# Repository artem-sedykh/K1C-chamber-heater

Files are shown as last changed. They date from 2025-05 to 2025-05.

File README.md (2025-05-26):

_# K1C-chamber-heater

Постоянно печатаю ABS, так что давно хотел сделать нагреватель камеры, пробовал разные варианты, например [такой](https://www.printables.com/make/2215362) на 24 вольта, выявил несколько проблем  
1. Обдув должен быть от улитки 12030
2. Знать температура нагревателя
3. Горячий воздух должен быть направлен на стекло(стенки плавятся)

Появилось время, наткнулся на видео [NoizieWorks](https://www.youtube.com/watch?v=dcIuKb0kHWA) нагреватель Qidi Plus 4, было принято решение попробовать собрать из него нагреватель для своего K1C  

И так, нам понадобится:

1. [QIDI Plus4 chamber heater](https://aliexpress.ru/item/1005007804483549.html?sku_id=12000042258968076) 4328 ₽.
2. [STM32-Klipper-Expander](https://aliexpress.ru/item/1005002384419036.html?sku_id=12000020472565357) 1359 ₽ плата расширения, доп. выходы, нужна для подключения нагревателя, термистора нагревателя и вентилятора
3. Винты 15x[M3x6 FHCS](https://aliexpress.ru/item/4001072025844.html)
4. Винты 3x[M3x40 FHCS](https://aliexpress.ru/item/4001072025844.html?sku_id=10000014059762471) для крепления вентилятора к корпусу нагревателя
5. Любая термопаста
6. Вплявляемые гайки 18xM3*3*4.5
7. Реле [SSR-40DA](https://aliexpress.ru/item/1005004040211802.html?sku_id=12000031095481981) 349 ₽
8. Провода 14awg протянуть до платы 220в(родных не хватит)
9. Провода для удлинения вентилятора
10. Провода для удлинения термистора
11. Коннектор [jst ph2.0 4pin](https://aliexpress.ru/item/1005008769943807.html) 
12. Обжимка для коннектора jst ph2.0 4pin
13. Кабель micro usb
14. [Набор инструментов для обжима и зачистки наконечников](https://www.ozon.ru/product/nabor-instrumentov-dlya-obzhima-i-zachistki-nakonechnikov-soderzhashchiy-odin-1813569243/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), если хотите обжать провода
15. [Кабельный наконечник НВИ](https://www.ozon.ru/product/kabelnyy-nakonechnik-nvi-dori-nabor-8-160sht-1416852199/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) ну и [пресс клещи ПК-16](https://www.ozon.ru/product/press-kleshchi-pk-16-dlya-mednyh-nakonechnikov-i-gilz-do-16kv-1566599786/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)
16. Катушка [Polymaker Fiberon PA6-GF25](https://fiberon.polymaker.com/product/pa6-gf25/) купить можно на [ozon](https://www.ozon.ru/product/pa6-gf25-fiberon-plastik-polymaker-dlya-3d-printera-1-75-mm-seryy-0-5-kg-1785755210/), у пластика тмпература деформации 190 градусов, кароч крутой материал  ~ 2300₽ за 0.5кг
17. Обычный abs для холодной части я использовал ERYONE ABS Carbon, брал [тут](https://www.ozon.ru/product/plastik-abs-carbon-cf-chernyy-black-dlya-3d-printera-eryone-1kg-1704937868/) ~ 2300₽ за 1кг
18. [Оплетка для проводов](https://www.ozon.ru/product/opletka-kabelnaya-iz-poliestera-zmeinaya-kozha-10-8-20mm-cherno-krasnaya-10m-1710567427/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)
19. TPU для печати заглушки для проводов

**Итого**: 4328+1359+2300+2300=10287₽ и это без учета обжимок и всякой мелочи, 10 раз думаем надо ли оно вам, если надо идем дальше.

### Прошивка Klipper-Expander
Подключаем Klipper-Expander к тачке на которой у нас есть linux  
клонируем репу клипера `git cone https://github.com/Klipper3d/klipper.git` и дальще по [инструкции](https://github.com/VoronDesign/Voron-Hardware/blob/master/Klipper_Expander/Documentation/Setup_and_Flashing_Guide.md) к Klipper-Expander

После прошивки можно подключить плату в usb принтера и проверить что все работает
Находим наш stm32 `ls /dev/serial/by-id/*` Добавляем секцию с нашим mcu
```yaml
[mcu expander]
serial: /dev/serial/by-id/usb-Klipper_stm32f042x6_1B0027001453303755373220-if00
restart_method: command
```
В информации о системе в fluidd мы его увидим

### Крепление Klipper-Expander
Для крепления я напечатал 2 стойки впаял в них гайки с одной и другой стороны, сделал в принтере 2 дырки и прикрутил, модельки не осталось, но думаю не проблема начертить цилиндр диарметром 6мм с дыркой 4мм  

Компановка корпуска выглядит так, у меня стол на 220, так что пришлось впихнуть 2 SSR

Я подключал Klipper-Expander к порту лидара, но если он используется, то можно подключить к порту usb, скорее всего флешками с g-кодом уже не польуются  
Отрезаем по размеру кабель, обжимаем его коннектором ph2.0, провода в кабеле по цветам такие же как на соседних портах, например от порта usb  

Так же надо подключить питание 24в которое будет подаваться на наши мосфеты на плате Klipper-Expander

### Подключение SSR
Подкючаем управляющие контакты к Klipper-Expander порты можно посмотреть в [документации](https://github.com/VoronDesign/Voron-Hardware/blob/master/Klipper_Expander/Documentation/README.md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)
Схема подключения SSR
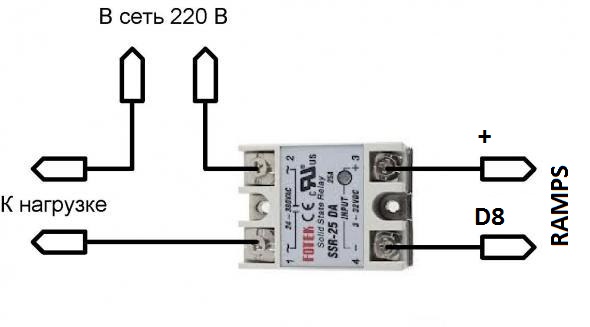
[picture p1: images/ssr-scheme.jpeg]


### Сборка корпуса
1. Вплавляем все гайки
2. Скручиваем горячую и холодную часть
3. Разбираем нареватель от QIDI Plus4
4. Вплавляем гайти в вентилятор 12030

5. Стираем термопасту, вытаскиваем термистр
6. Переклеиваем каптоновый скотч в новый корпус засовываем термистр, наносим термопасту, ставим нагреватель
7. Вставляем вентилятор 
8. Утсанавливаем заглушку

### Установка в корпус
Снимаем боковые стенки, примеряем место для утстановки, корпус крепится на 3 винта, так что надо сделать еще 3 дырки в задней крышке принтера, задняя часть холодной части корпуса можно использовать как шаблон  
Протягиваем провода черех кбель каналы в подвал принтера, подключаем термистр, нагреватель на 220 и вентилятор, обрезаем провода по размеру, опресовываем.

*Вообще перед установкой просто подключите все без проводки в корпусе, проверьте что все работает*

### Конфиг
```yaml
---
[mcu expander]
serial: /dev/serial/by-id/usb-Klipper_stm32f042x6_1B0027001453303755373220-if00
restart_method: command
[temperature_sensor chamber_probe]
sensor_type: NTC 100K MGB18-104F39050L32
sensor_pin: expander:PA6
min_temp: -100
max_temp: 140

[heater_generic chamber]
heater_pin: expander:PA3
max_power: 0.6
# https://github.com/qidi-community/Plus4-Wiki/blob/main/content/chamber-heater-investigation/README.md
sensor_type: temperature_combined
sensor_list: temperature_sensor nozzle_mcu_temp, temperature_sensor chamber_temp, temperature_sensor chamber_probe, temperature_sensor chamber_temp
combination_method: mean
maximum_deviation: 90
control = pid
pid_Kp=63.418 
pid_Ki=1.342 
pid_Kd=749.125
min_temp: -100
max_temp: 80

[verify_heater chamber]
max_error: 400
check_gain_time: 600
hysteresis: 5
heating_gain: 2

[heater_fan chamber]
pin: expander:PA0
heater: chamber
heater_temp: 45
```

Из настройки видно что использвется комбинированный датчки температуры, почему так написано [тут](https://github.com/qidi-community/Plus4-Wiki/blob/main/content/chamber-heater-investigation/README.md)  
У меня родной термистор камеры закрыт [крышкой](https://www.printables.com/model/1167584-creality-k1k1ck1-max-chamber-thermistor-cover) и я получал с него температуру пластика, а не воздуха
А поднимать температуру воздуха который идет с нагревателя нельзя поднимать выше 85 градусов, иначе у нас перегреется mcu головы, так что нам надо получить заданную тмпературу именно воздуха 
Калибровать значение можно температурой сопла когда оно холодное, включаем вентилятор обдува модели и смотрим показание с нагревателя котороый берет медианное значение со списка сенсоров.

### Результаты
12-15 минут прогрев воздуха в принтере до 65 градусов при столе в 90
Когда была не правильно настроена температура грел принтер до 90, торубалась mcu головы.
Тесты на прочность не проводил, по факту уменьшил температуру стора для abs с 105 до 90

Фотки нагретого принтера термокамерой

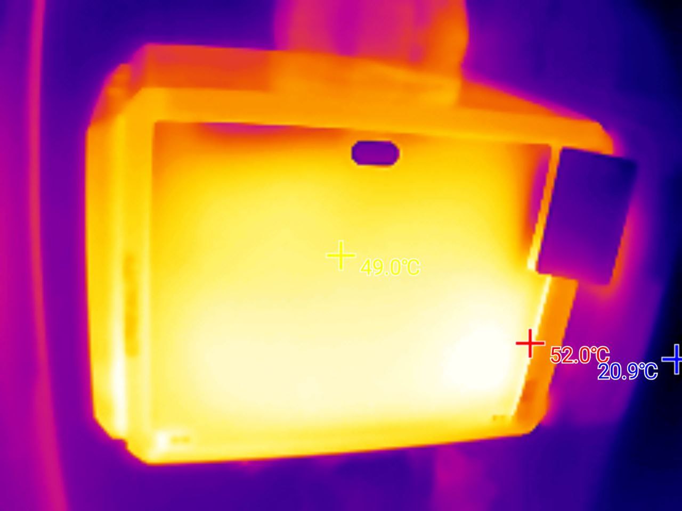
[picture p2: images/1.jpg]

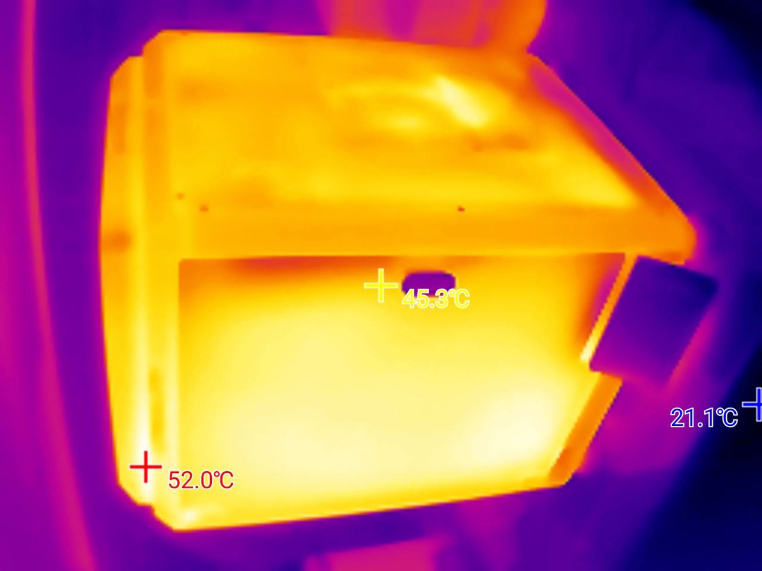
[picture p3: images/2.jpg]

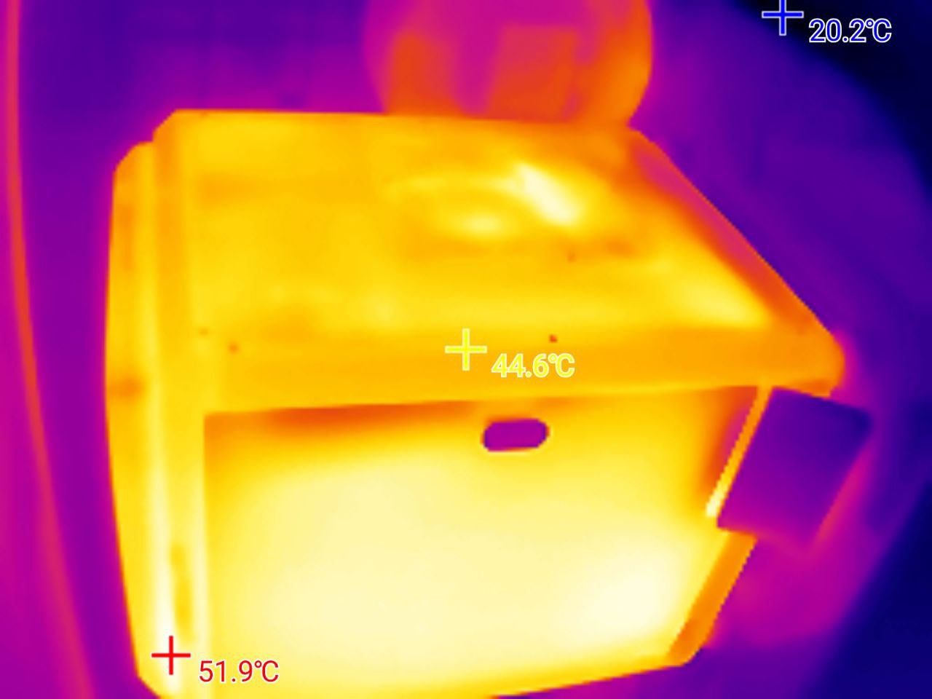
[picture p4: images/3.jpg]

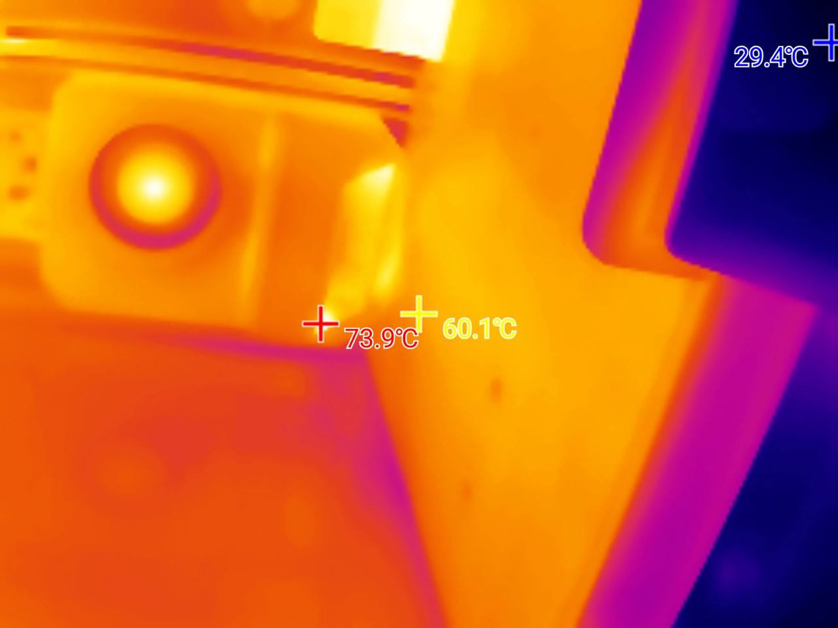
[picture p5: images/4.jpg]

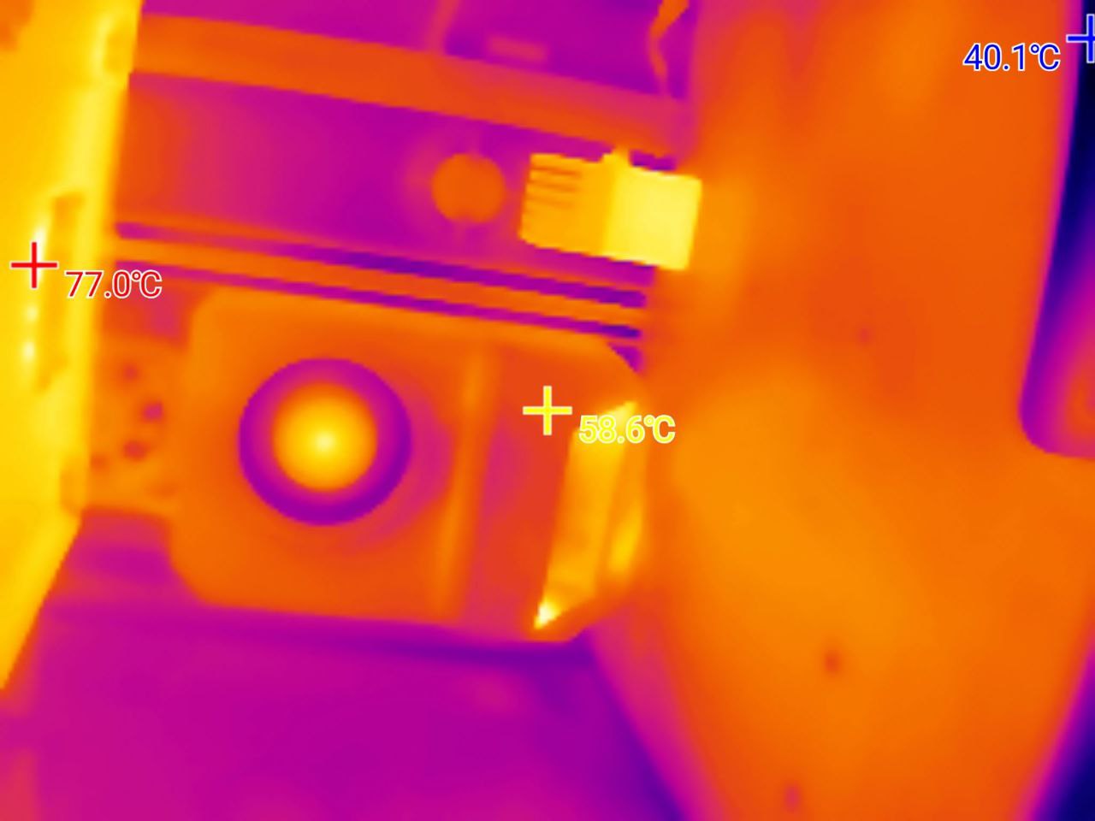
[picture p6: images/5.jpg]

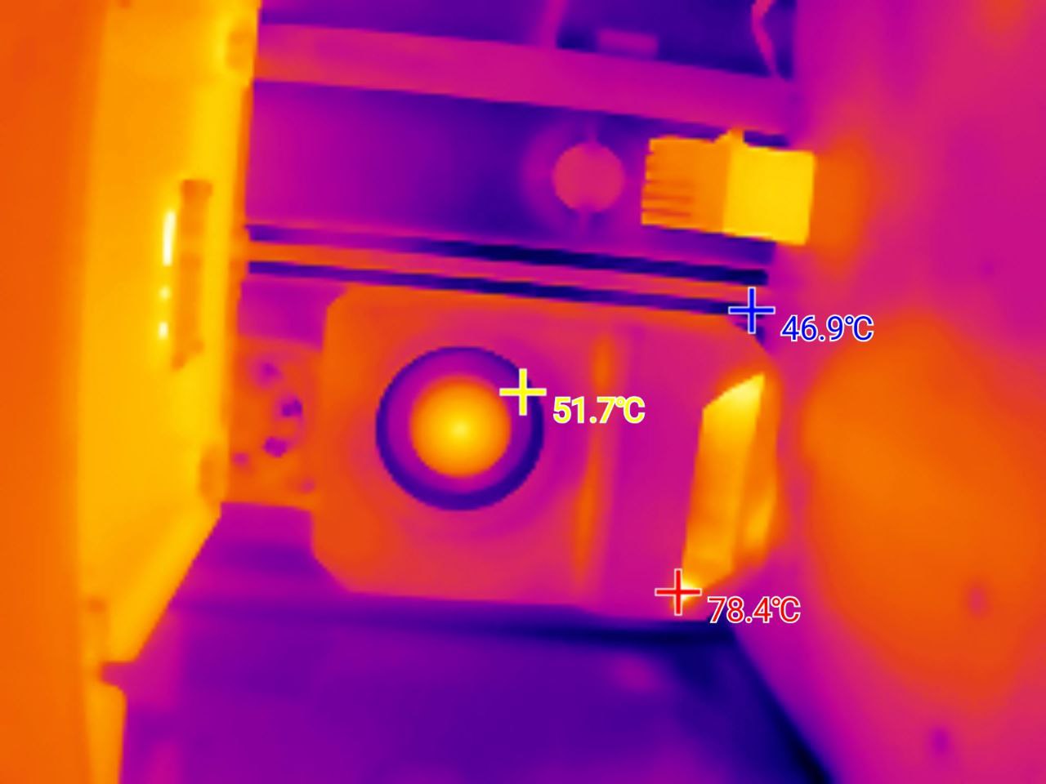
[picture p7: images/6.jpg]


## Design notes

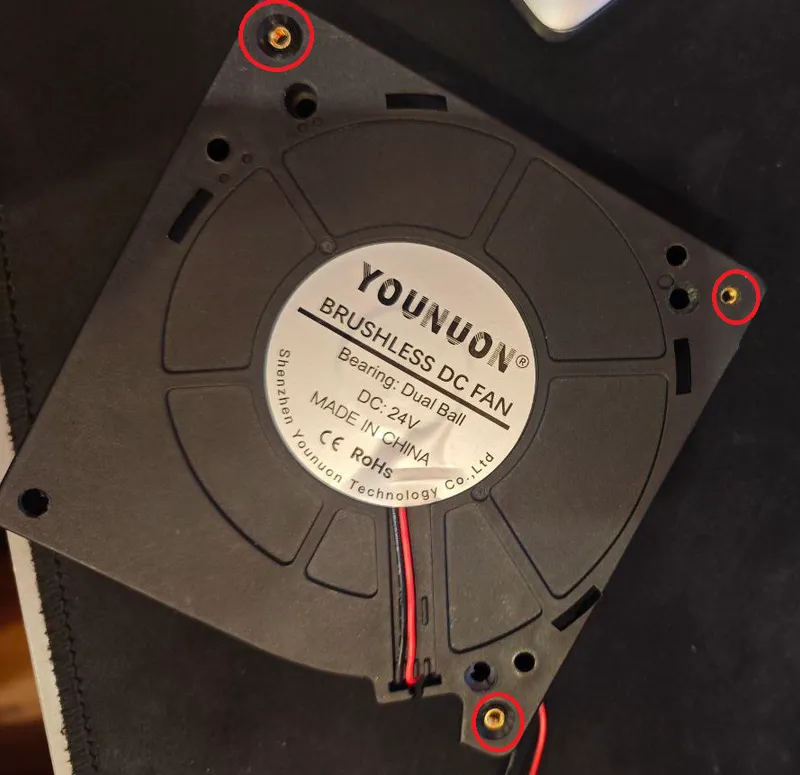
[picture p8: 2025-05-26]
images/img.png

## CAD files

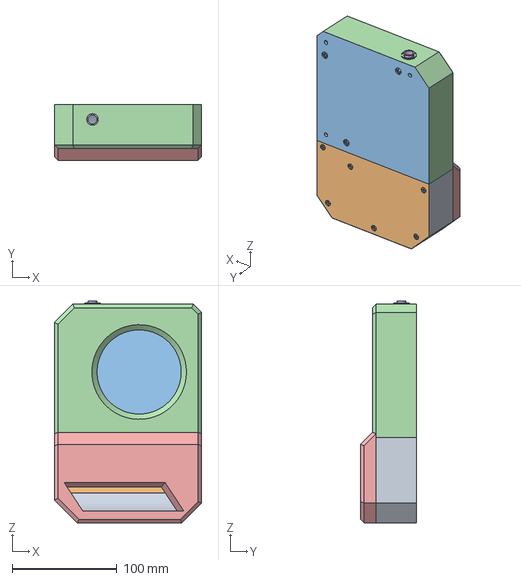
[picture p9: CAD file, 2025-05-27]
CAD/k1-series-chamber-heater-v1.step
140.4 x 53.5 x 211.6 mm
